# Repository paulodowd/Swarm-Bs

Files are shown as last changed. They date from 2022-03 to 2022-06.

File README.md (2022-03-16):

# Swarm-Bs (work in progress)

## Features

- Can be considered a general purpose I2C extension board to provide local infra-red (IR) communication.
- Can also be used stand-alone (example code to come).
- IR Serial transmission at 4800 Baud.
- Transmit/receive upto 28 bytes (currently, extensible).
- Range can be reduced/set with a trimmer potentiometer.
- Message corruption detection implemented with a CRC checksum.
- Designed to conveniently fit to an expansion header of the Pololu 3Pi+ mobile robot.

## Summary

This board is a revised version of the 3Pi_IRComm board. Rather than updating the 3Pi_IRComm repository, it seemed like this board was different enough to have it's own - this way the simpler 3Pi_IRComm board design can persist.  However, this board can be taken as a better design, and unwanted components simply left unpopulated.  The fabrication cost of the PCB is essentially the same.

The board has been revised to include more functionality, especially for human interaction.  The board is intended to now be suitable for both the Pololu 3Pi+ robot and to fit against a wall mounted display.  

Significant changes include:
- It uses an Arduino Nano (rather than an Arduino Pro Mini).
- includes 1 Light Dependent Resistor (LDR).
- includes 3 Potentiometers.
- includes 1 Button.
- includes 1 RGB LED.
- includes a Polarity protection diode.
- includes some necessary resistors.

The Arduino Nano has been used (instead of the pro mini) because it has a built-in USB connector and so is more readily programmable.  This decision was made because these boards may be used as stand-alone devices in classroom workshops - therefore, the firmware isn't necessarily so fixed.  

## Important Considerations

## Bill of Materials (BOM)

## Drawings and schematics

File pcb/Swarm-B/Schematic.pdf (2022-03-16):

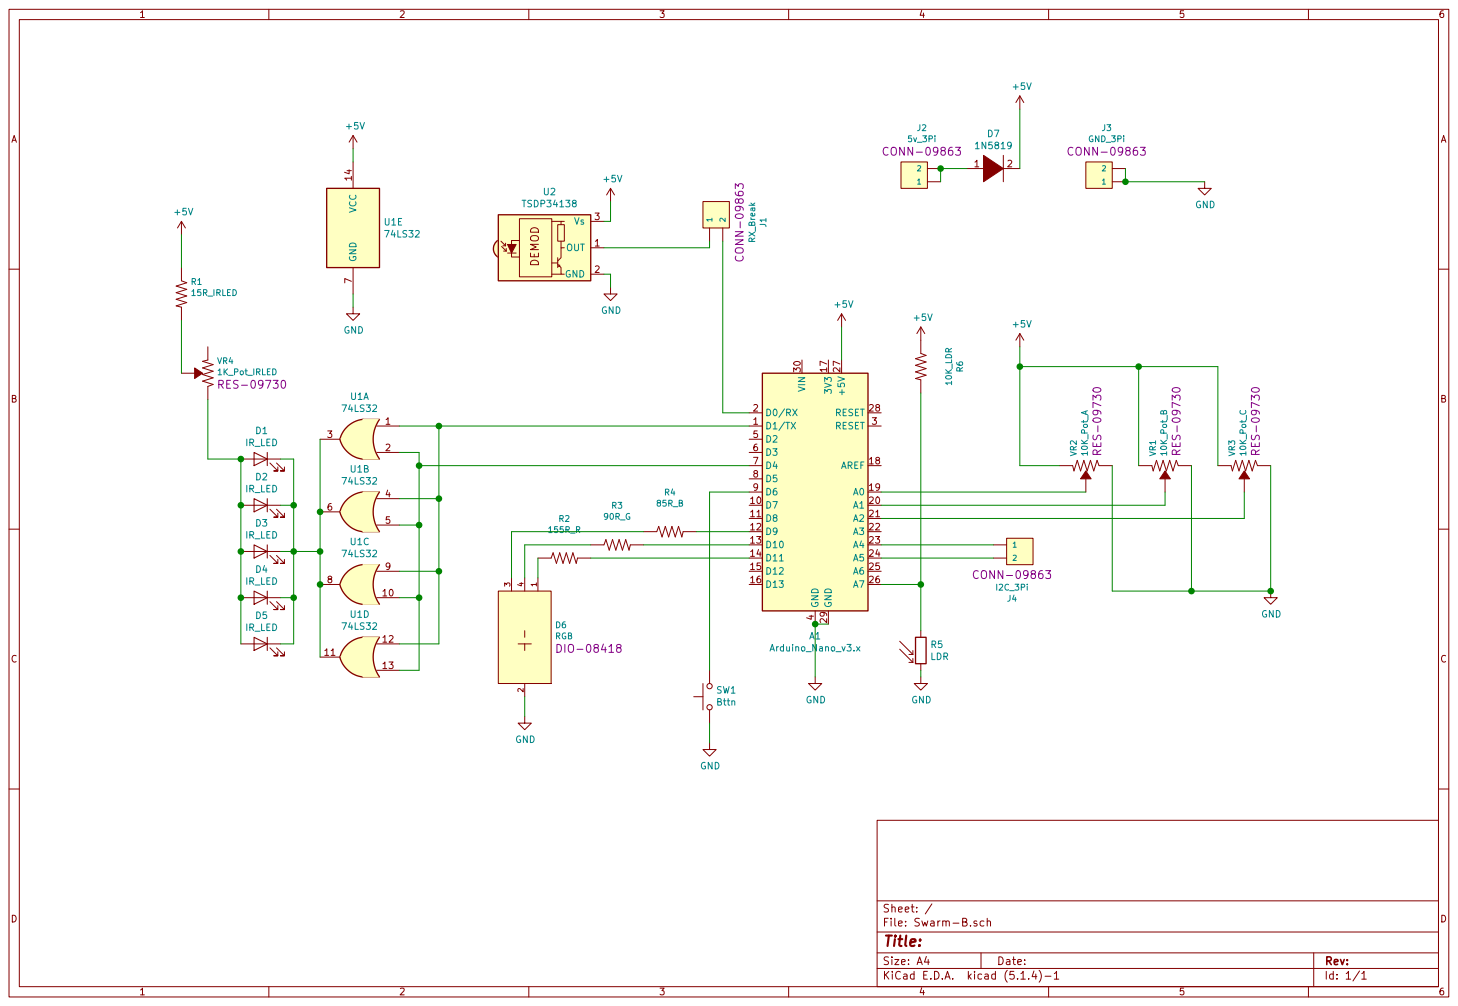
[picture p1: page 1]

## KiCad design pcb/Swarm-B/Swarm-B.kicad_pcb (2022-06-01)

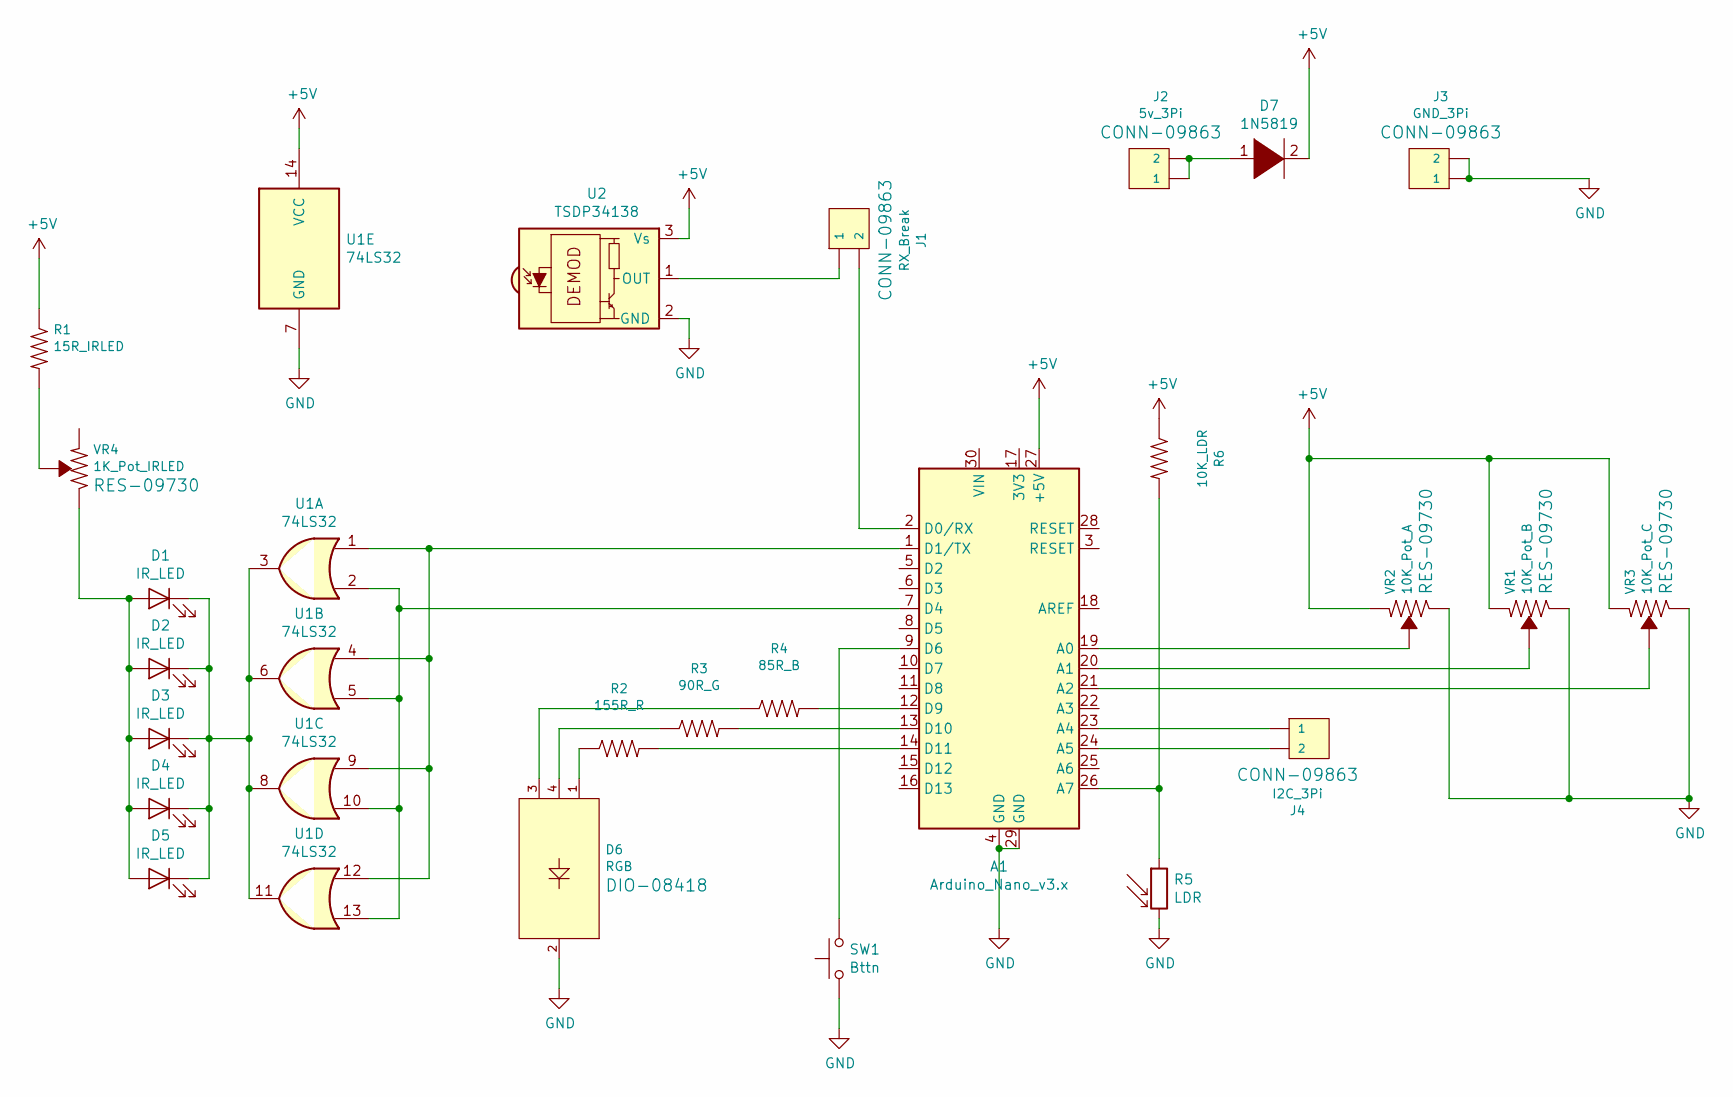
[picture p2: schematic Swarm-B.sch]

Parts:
A1: Arduino_Nano_v3.x; Arduino_Nano
D1, D2, D3, D4, D5: IR_LED; LED_D3.0mm_Horizontal_O1.27mm_Z2.0mm
D6: RGB; LED_D5.0mm-4_RGB
D7: 1N5819; D_DO-34_SOD68_P7.62mm_Horizontal
J1: RX_Break; PinHeader_1x02_P2.54mm_Vertical
J2: 5v_3Pi; PinHeader_1x02_P2.54mm_Vertical
J3: GND_3Pi; PinHeader_1x02_P2.54mm_Vertical
J4: I2C_3Pi; PinHeader_1x02_P2.54mm_Vertical
R1: 15R_IRLED; R_Axial_DIN0204_L3.6mm_D1.6mm_P7.62mm_Horizontal
R2: 155R_R; R_Axial_DIN0204_L3.6mm_D1.6mm_P7.62mm_Horizontal
R3: 90R_G; R_Axial_DIN0204_L3.6mm_D1.6mm_P7.62mm_Horizontal
R4: 85R_B; R_Axial_DIN0204_L3.6mm_D1.6mm_P7.62mm_Horizontal
R5: LDR; R_LDR_5.0x4.1mm_P3mm_Vertical
R6: 10K_LDR; R_Axial_DIN0204_L3.6mm_D1.6mm_P7.62mm_Horizontal
SW1: Bttn; SW_PUSH_6mm
U1: 74LS32; DIP-14_W7.62mm_Socket
U2: TSDP34138; Vishay_MOLD-3Pin
VR1: 10K_Pot_B; Potentiometer_Bourns_3386F_Vertical
VR2: 10K_Pot_A; Potentiometer_Bourns_3386F_Vertical
VR3: 10K_Pot_C; Potentiometer_Bourns_3386F_Vertical
VR4: 1K_Pot_IRLED; Potentiometer_Bourns_3386P_Vertical

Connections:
+5V: A1.27 (+5V), D7.2 (A), R1.1, R6.1, U1.14 (VCC), U2.3 (Vs), VR1.1 (CCW), VR2.1 (CCW), VR3.1 (CCW)
GND: A1.4 (GND), A1.29 (GND), D6.2 (C), J3.1, J3.2, R5.2, SW1.1, U1.7 (GND), U2.2 (GND), VR1.3 (CW), VR2.3 (CW), VR3.3 (CW)
unnamed: A1.1 (D1/TX), U1.1, U1.4, U1.9, U1.12
unnamed: A1.2 (D0/RX), J1.2
unnamed: A1.7 (D4), U1.2, U1.5, U1.10, U1.13
unnamed: A1.9 (D6), SW1.2
unnamed: A1.12 (D9), R4.2
unnamed: A1.13 (D10), R3.2
unnamed: A1.14 (D11), R2.2
unnamed: A1.19 (A0), VR2.2 (WIPER)
unnamed: A1.20 (A1), VR1.2 (WIPER)
unnamed: A1.21 (A2), VR3.2 (WIPER)
unnamed: A1.23 (A4), J4.1
unnamed: A1.24 (A5), J4.2
unnamed: A1.26 (A7), R5.1, R6.2
unnamed: D1.1 (K), D2.1 (K), D3.1 (K), D4.1 (K), D5.1 (K), U1.3, U1.6, U1.8, U1.11
unnamed: D1.2 (A), D2.2 (A), D3.2 (A), D4.2 (A), D5.2 (A), VR4.3 (CW)
unnamed: D6.1 (RED), R2.1
unnamed: D6.3 (GRN), R4.1
unnamed: D6.4 (BLU), R3.1
unnamed: D7.1 (K), J2.1, J2.2
unnamed: J1.1, U2.1 (OUT)
unnamed: R1.2, VR4.2 (WIPER)

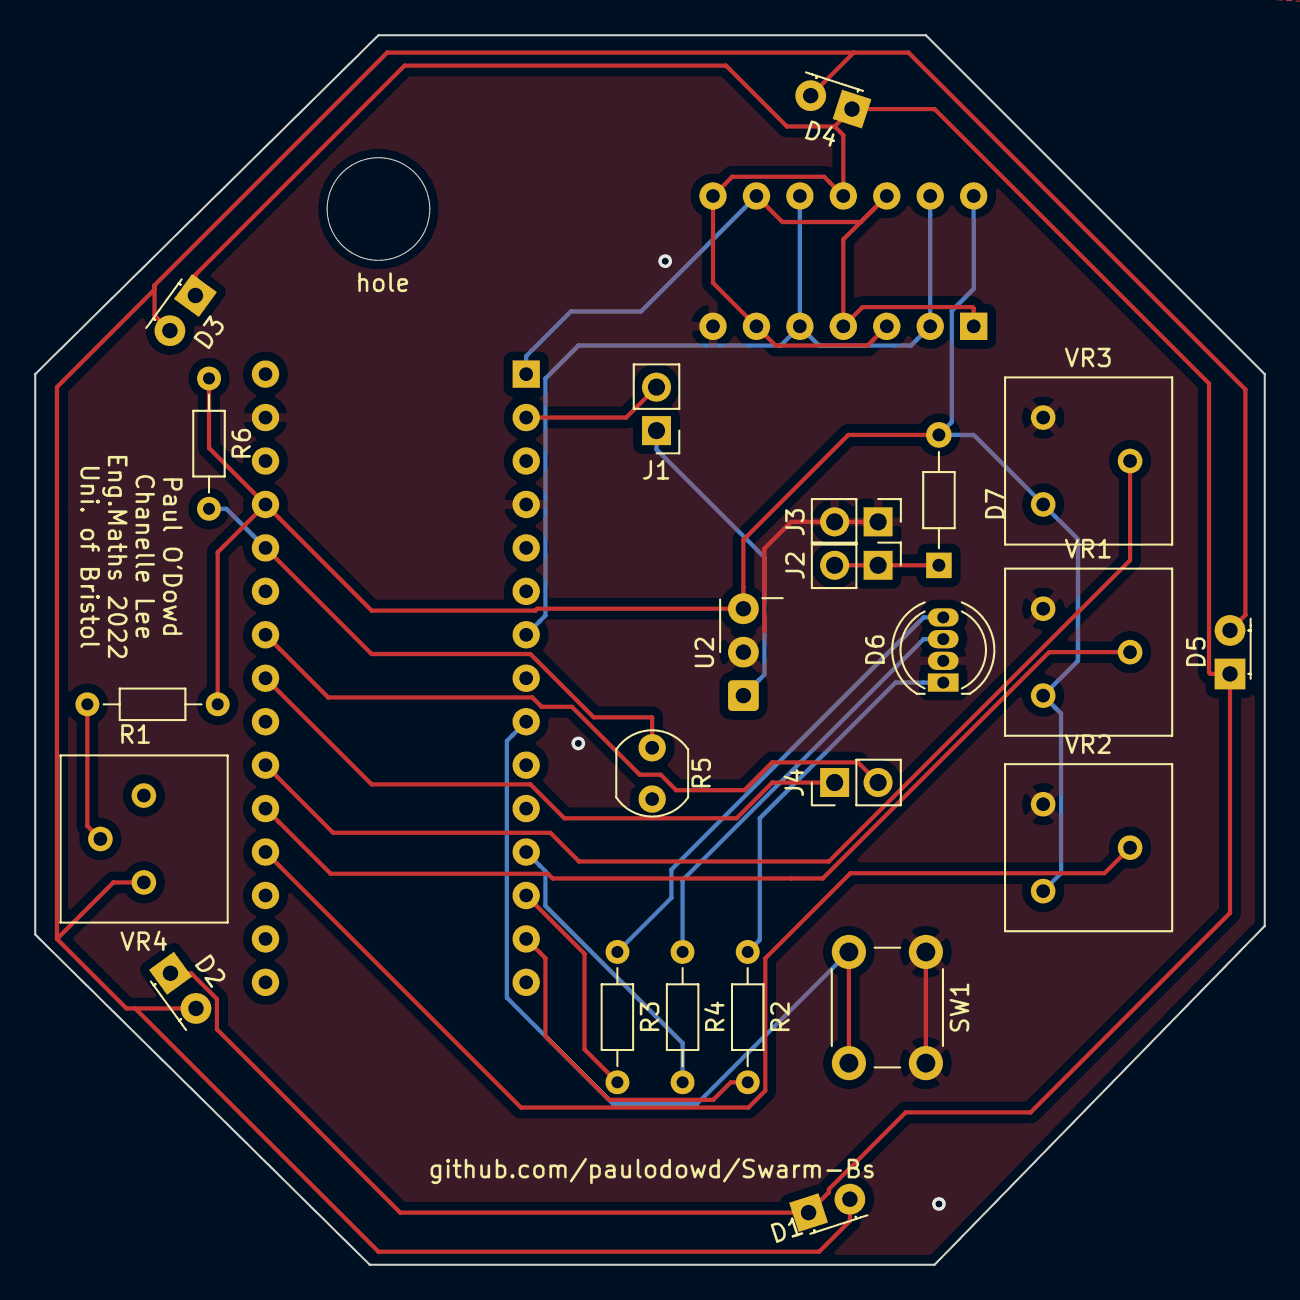
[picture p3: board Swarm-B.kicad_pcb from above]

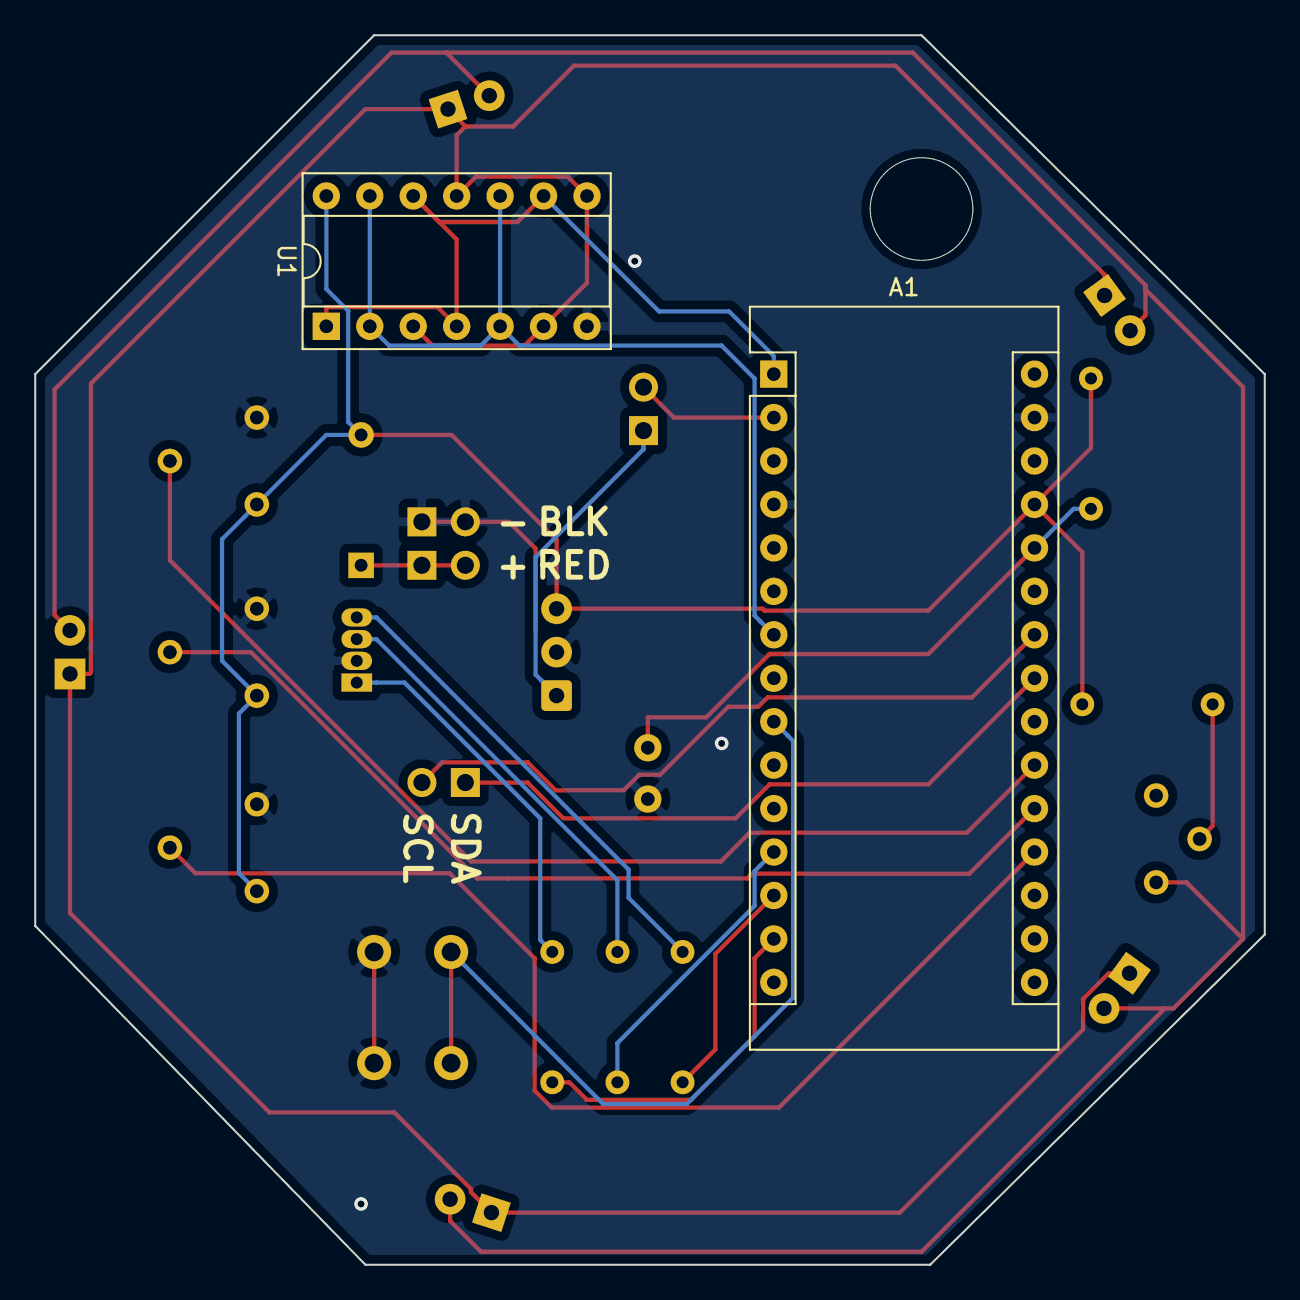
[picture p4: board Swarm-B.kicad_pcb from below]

Board: 2 copper layers, 71.9 x 71.9 mm, 26 parts (2 on the bottom side), 23 nets.

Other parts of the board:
hole: hole; MountingHole_6mm

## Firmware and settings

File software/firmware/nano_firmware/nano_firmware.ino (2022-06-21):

/*
   i2c slave device to handle IR messaging between
   3pi+ robots.
*/
#include <avr/io.h>
#include <Wire.h>
#define I2C_ADDR 8

boolean LED;      // debug LED
unsigned long ts; // general time stamp, timeout for
// debug LED.

#define POT_A A0
#define POT_B A1
#define POT_C A2

// Two operational states
#define STATE_IR_TX_ON 1
#define STATE_IR_TX_OFF 2
int state = STATE_IR_TX_ON;


#define MAX_MSG 32
static char tx_buf[MAX_MSG];  // buffer for IR out (serial)
static char rx_buf[MAX_MSG];  // buffer for IR in  (serial)
static char rx_msg[MAX_MSG];  // holding buffer for msg down
// to Master over i2c
int rx_count;

// 38Khz signal generated on
// digital pin 4.
#define TX_CLK_OUT 4

unsigned long msg_ttl; // msg time to live
#define TTL 1000       // keep a message for 1 second
// then delete.

unsigned long tx_ts;    // transmit time-stamp
unsigned long tx_delay; // delay between tx

// Flags
boolean BROADCAST = false;
boolean PROCESS_MSG = false;
#define LED_B 9
#define LED_G 10
#define LED_R 11



void setup() {

  // Set random seed.
  initRandomSeed();

  // Set pin for 38khz carrier as output
  pinMode(TX_CLK_OUT, OUTPUT);

  // Debug led
  pinMode(13, OUTPUT);

  // RGB LED
  pinMode( LED_R, OUTPUT );
  pinMode( LED_G, OUTPUT );
  pinMode( LED_B, OUTPUT );

  // Input pots
  pinMode( POT_A, INPUT );
  pinMode( POT_B, INPUT );
  pinMode( POT_C, INPUT );

  // Set message buffers to invalid (empty) state
  memset( tx_buf, 0, sizeof( tx_buf ));
  memset( rx_buf, 0, sizeof( rx_buf ));
  memset( rx_msg, 0, sizeof( rx_msg ));



  // Setup Timer 2 to help generate a 38khz signal.
  setupTimer2();

  // Begin I2C, note, as a slave device.
  Wire.begin( I2C_ADDR );
  Wire.onRequest( reportLastMessage );
  Wire.onReceive( newMessageToSend );

  // Start Serial.  Note, here we are using
  // serial to transmit strings over IR by
  // modulating it with the 38khz carrier.
  // The IR demodulator chip can support
  // baud up to 4800, but other variants
  // might not.
  Serial.begin(4800);
  Serial.setTimeout(500);

  // Set initial time-stamp values
  ts = millis();
  msg_ttl = millis();

  tx_ts = millis();
  setTXDelay();
  //disableTX();
  resetRxBuf();
}


// Experiment to see if reading the LSB
// of an analog read can generate a
// useful random seed.  Nothing connected
// to A0.  I think the LSB fluctuates
// randomly(?)
void initRandomSeed() {
  pinMode(A0, INPUT);
  byte r = 0x00;
  for ( int i = 0; i < 8; i++ ) {
    byte b = (byte)analogRead(A0);
    b = b & 0x01;
    r |= (b << i);
    delayMicroseconds(2);
  }
  randomSeed( r );
}

// Attempting an asynchronous send
// and listen procedure because we
// can't do both at the same time.
// https://lucidar.me/en/serialib/most-used-baud-rates-table/
// We are using 4800 baud, which is
// 4800 bits per second.
// 1.042ms per byte.
// So we space transmission by 64ms
// to allow for receipt, and pad/vary
// by upto 50ms(?)
void setTXDelay() {
  float t = (float)random(0, 50);
  t += 64;
  // Insert random delay to help
  // break up synchronous tranmission
  // between robots.
  tx_delay = (unsigned long)t;
}

void setRGB( int r, int g, int b ) {
  if ( r == 0 ) {
    digitalWrite( LED_R, LOW );
  } else {
    digitalWrite( LED_R, HIGH );
  }

  if ( g == 0 ) {
    analogWrite( LED_G, 0 );
  } else {
    analogWrite( LED_G, g );
  }


  if ( b == 0 ) {
    analogWrite( LED_B, 0 );
  } else {
    analogWrite( LED_B, b );
  }

}

// This ISR simply toggles the state of
// pin D4 to generate a 38khz clock signal.
ISR( TIMER2_COMPA_vect ) {
  PORTD ^= (1 << PD4);

}

// We use Timer2 to generate a 38khz clock
// which is electronically OR'd with the
// serial TX.
void setupTimer2() {

  // Termporarily stop interupts
  cli();

  // Setup Timer 2 to fire ISR every 38khz
  // Enable CTC mode
  TCCR2A = 0;
  TCCR2A |= (1 << WGM21);

  // Setup ctc prescaler
  TCCR2B = 0;

  // No prescale?
  //TCCR2B |= (1<<CS21);
  TCCR2B |= (1 << CS20);

  // match value
  OCR2A = 210; // counts to 53, every 38,000hz
  //OCR2A = 53; // counts to 53, every 38,000hz


  // Set up which interupt flag is triggered
  TIMSK2 = 0;
  TIMSK2 |= (1 << OCIE2A);

  // enable interrupts
  sei();

}


byte CRC( String in_string ) {
  String buf;
  byte cs;
  int i;

  cs = 0;
  for ( i = 0;  i < (int)in_string.length(); i++ ) {
    cs = cs ^ in_string.charAt(i);
  }
  cs &= 0xff;

  return cs;
}

// Over i2c to Master
// Sends a string of the latest message received from
// other robots.
// If the buffer is empty, a ! character is sent.
// Note, a correct message should also end in !
void reportLastMessage() {

  // No message.
  if ( rx_msg[0] == 0 ) {
    Wire.write("!");
  } else {
    Wire.write( rx_msg, strlen(rx_msg) );
  }

}

// For IR.
// Function to format a message for our
// IR transmission.  We use:
// * to indicate the start of a message
// @ to indicate a checksum value following
void newMessageToSend( int len ) {

  char buf[MAX_MSG];

  //Serial.println(len);
  //digitalWrite(13, HIGH);
  int count = 0;

  // Stop transmission whilst we update
  // the buffer.
  state = STATE_IR_TX_OFF;

  // Clear tx buffer
  memset( buf, 0, sizeof( buf ) );

  // set first character as our message
  // start byte
  buf[count++] = '*';

  // Should we add a timeout here?
  // Receive up until buffer -1
  while ( Wire.available()  ) {
    char c = Wire.read();
    buf[count] = c;
    count++;
  }

  // If it is a malformed message from the robot,
  // or the ! symbol
  // we clear the tx_buf and so stop sending messages
  if ( count <= 1 || buf[1] == '!' ) {
    //Serial.println(" Cleared");
    memset( tx_buf, 0, sizeof( tx_buf ) );

    // If we received RGB,n,n,n then we attempt to parse and set the RGB LED
  } else if ( count >= 4 ) {


    if ( buf[1] == 'R' && buf[2] == 'G' && buf[3] == 'B' ) {

      
      // Get R G and B values
      char * substrings[5];
      char * ptr;
      byte index = 0;
      ptr = strtok( buf, ",");
      while ( ptr != NULL && index <= 4 ) {
        substrings[index] = ptr;

        index++;
        ptr = strtok( NULL, ",");
      }

      // found 4 substrings? [rgb,n,n,n]
      if ( index == 4 ) {
        int r = atoi( substrings[1] );
        int g = atoi( substrings[2] );
        int b = atoi( substrings[3] );
        setRGB( r, g, b );
      }

    } else {
      // copy new tx message into correct
      // buffer.
      memset( tx_buf, 0, sizeof( tx_buf ) );
      for ( int i = 0; i < count; i++ ) {
        tx_buf[i] = buf[i];
      }

      // Add crc
      byte cs;
      int i;

      cs = 0;
      for ( i = 0;  i < count; i++ ) {
        cs = cs ^ tx_buf[i];
      }
      cs &= 0xff;

      tx_buf[count++] = '@';
      tx_buf[count++] = cs;
      //Serial.println("Set");
    }

  } else {
    // copy new tx message into correct
    // buffer.
    memset( tx_buf, 0, sizeof( tx_buf ) );
    for ( int i = 0; i < count; i++ ) {
      tx_buf[i] = buf[i];
    }

    // Add crc
    byte cs;
    int i;

    cs = 0;
    for ( i = 0;  i < count; i++ ) {
      cs = cs ^ tx_buf[i];
    }
    cs &= 0xff;

    tx_buf[count++] = '@';
    tx_buf[count++] = cs;
    //Serial.println("Set");
  }








  //Serial.println( count );
  //Serial.println( tx_buf );

  // Restart IR transmission
  state = STATE_IR_TX_ON;
}


// The arduino pro mini has a parallel serial
// interface,meaning with IR it can receive
// it's own tranmission. There, we access the
// UART register to disable RX functionality.
// When we re-enable it, this has the beneficial
// side-effect of clearing the input buffer.

void disableRX() {
  cli();
  UCSR0B &= ~( 1 << RXEN0 );
  UCSR0B &= ~( 1 << RXCIE0 );
  sei();
}

// Re-enable the serial port RX hardware.
void enableRX() {


  cli();
  UCSR0A &= ~(1 << FE0);
  UCSR0A &= ~(1 << DOR0);
  UCSR0A &= ~(1 << UPE0);
  UCSR0B |= ( 1 << RXEN0 );
  UCSR0B |= ( 1 << RXCIE0 );
  sei();
}

// Clears our received buffer
void resetRxBuf() {
  rx_count = 0;
  PROCESS_MSG = false;
  memset( rx_buf, 0, sizeof( rx_buf ) );
}



void loop() {



  // Toggle whether we are broadcasting
  // or listening for IR messages
  if ( millis() - tx_ts > tx_delay ) {
    BROADCAST = !BROADCAST;
    tx_ts = millis();

    // Set a different delay for next
    // iteration
    setTXDelay();
  }


  // If we are in broadcast mode and the LEDS
  // are active.
  if ( state == STATE_IR_TX_ON && BROADCAST) {

    // If we have not received a message from
    // the Master over i2c, do nothing.
    if ( strlen(tx_buf) == 0 ) {
      // don't send, empty buffer.

    } else { // Message from Master to send.

      // We have a problem where we pick up
      // our own reflected transmission.
      disableRX();


      // Using Serial.print transmits over
      // IR.  Serial TX is modulated with
      // the 38Khz carrier in hardware.
      Serial.println( tx_buf );
      Serial.flush(); // wait for send to complete


      // With TX finished, we can receive again
      // and not get our own transmission.
      enableRX();

    }
  }


  // Clear old messages received via IR.
  if ( millis() - msg_ttl  > TTL ) {
    memset( rx_msg, 0, sizeof( rx_msg ) );
    msg_ttl = millis();
  }

  // Clear status LED
  if ( millis() - ts > 100 ) {
    ts = millis();
    digitalWrite( 13, LOW );
    //setRGB( 1, 0, 0 );


    // Debug
    //Serial.print("last message: ");
    //Serial.print( rx_msg );
    //Serial.print(" ");
    //Serial.println( ts );
  }


  // See if we have received over IR to
  // process.
  while ( Serial.available() && !PROCESS_MSG ) {

    // If we find a newline, we flag we have
    // a message to attempt to process.
    rx_buf[rx_count] = Serial.read();
    if ( rx_buf[ rx_count ] == '\n' ) PROCESS_MSG = true;


    // Note that, it might seem like rx_count will
    // exceed the buffer. The next check should
    // catch this, and cause the buffer to be
    // processed.  We don't zero rx_count on each
    // call of loop() because we may only have a
    // few characters in the Serial buffer.  So we
    // need to incrementally fill our rx_buf with
    // many calls to this while loop.
    // Processing the message will reset rx_count
    // to 0.
    rx_count++;

    // If we exceed the buffer size, we also
    // will try to process the message.
    if ( rx_count >= MAX_MSG ) PROCESS_MSG = true;
  }

  // Do we think we have a message to process?
  if ( PROCESS_MSG ) {

    // Debug
    //Serial.print("got "); Serial.print(rx_buf); Serial.print(":"); Serial.println(rx_count);

    // Invalid conditions:
    if ( rx_count <= 0 || rx_buf[0] == 0 ) {
      // bad read.
      //Serial.println("bad serial");


    } else {  // Valid rx buf

      // Check for start byte
      int start = -1;  // -1 = default error state

      // Search string for * symbol (start)
      // Save index
      for ( int i = 0; i < rx_count; i++ ) {
        if ( rx_buf[i] == '*') {
          start = i;
          break;
        }
      }

      // Message too short or bad
      // e.g. a good message would be:
      //      *abcdef@a  (start,message,CRC token, CRC value)
      //      a useless message would be:
      //      minimum (absurd) message would be *@_
      //      min message length = 3
      // if start < 0, then no * symbol was found
      if ( (rx_count - start) <= 3 || start < 0 ) {
        //Serial.println("message too short :(");

      } else { // message valid, * index found

        // Check CRC, find @ token to separate
        // out CRC value.
        int last = -1;
        for ( int i = 0; i < rx_count; i++ ) {
          if ( rx_buf[i] == '@') {
            last = i;
            break;
          }
        }

        // Start should be 0 or more
        // Note, we include the start byte *
        // in the checksum
        if ( last > start && last < (rx_count - 1) ) {
          char buf[rx_count];
          int b = 0;  // count how many bytes

          // we copy.
          for ( int i = start; i < last; i++ ) {
            buf[b] = rx_buf[i];
            b++;
          }

          // We need at least 1 byte of data
          // between start and checksum
          if ( b >= 1 ) {
            //Serial.print("copied: " );
            //Serial.print( buf );
            //Serial.print( " b = ");
            //Serial.println(b);

            // Reconstruct checksum
            byte cs;
            cs = 0;
            for ( int i = 0;  i < b; i++ ) {
              cs = cs ^ buf[i];
            }
            cs &= 0xff;

            if ( cs == rx_buf[last + 1] ) {

              // Debug
              //Serial.println("CRC GOOD!");

              // Flash so we can see when robots are
              // receiving messages correctly
              digitalWrite(13, HIGH );
              //analogWrite(LED_R, 0 );
              //analogWrite(LED_G, 255);
              //setRGB( 0, 1, 0 );

              // Make sure where we will store this
              // received message is clear.
              memset( rx_msg, 0, sizeof( rx_msg ));

              // Copy message across, ignoring the *
              for ( int i = 0; i < b - 1; i++ ) {
                rx_msg[i] = buf[i + 1];
              }

              // Add a ! to the message, which will be
              // used when later sending down I2C to
              // the Master to indicate the end of the
              // string.
              rx_msg[b - 1] = '!';

              // Reset TTL timestamp, so this message
              // will only exist temporarily.
              msg_ttl = millis();

            } else {
              //Serial.println("CRC BAD!");
            }
          } else {
            //Serial.println("Message payload < 1 ");
          }

        }
      }
    }

    // reset receive
    resetRxBuf();

  }
} // end of loop

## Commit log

2022-03-16 added sda and scl labels to pcb
    [Swarm-B.kicad_pcb]
2022-03-17 update to readme
    [Swarm-B.kicad_pcb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]
2022-06-01 altered pcb to house ICs on the underside
    [Swarm-B.kicad_pcb, Swarm-B.sch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]
2022-06-09 added arduino nano firmware
    [Swarm-B-B_Mask.gbr, Swarm-B-F_Mask.gbr]
